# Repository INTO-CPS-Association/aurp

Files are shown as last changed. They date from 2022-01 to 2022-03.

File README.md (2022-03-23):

# Aarhus University Robotics Platform (AURP) Overview

## System
The system comprises:
- ODrive [D6374](https://eu.odriverobotics.com/shop/odrive-custom-motor-d6374-150kv) 150 KV BLDC motor
  - CUI [AMT102-V](https://www.cuidevices.com/product/resource/amt10.pdf) encoder - 8192 CPR quadrature with a single index mark
  - Thermistor (NTC 10k 1% 3435) thermally connected to motor windings to permit temperature monitoring
- ODrive [D5065](https://eu.odriverobotics.com/shop/odrive-custom-motor-d5065) 270 KV BLDC motor
  - CUI [AMT102-V](https://www.cuidevices.com/product/resource/amt10.pdf) encoder - 8192 CPR quadrature with a single index mark
  - Thermistor (NTC 10k 1% 3435) thermally connected to motor windings to permit temperature monitoring

_For detailed information on the D6374 and D5065 motors, see the [ODrive motor guide](https://docs.google.com/spreadsheets/d/12vzz7XVEK6YNIOqH0jAz51F5VUpc-lJEs3mmkWP1H4Y/edit#gid=0) ([PDF export](https://github.com/INTO-CPS-Association/aurp/blob/main/resources/ODrive_motor_guide.pdf) from 23-03-2022)_

- ODrive [V3.6 control board](https://eu.odriverobotics.com/shop/odrive-v36) - 56 V with connectors
  - 50 W power resistor (measured resistance of 2 &Omega;)
  - 2x Noctua [NF-A4x20 5V PWM](https://noctua.at/en/products/fan/nf-a4x20-5v-pwm) fan
- Mean Well [UHP-1000-48](https://www.meanwell.com/webapp/product/search.aspx?prod=UHP-1000) 1000 W / 48 V DC (21 A) power supply configured with 3x XT-60 connectors

<p align="center">
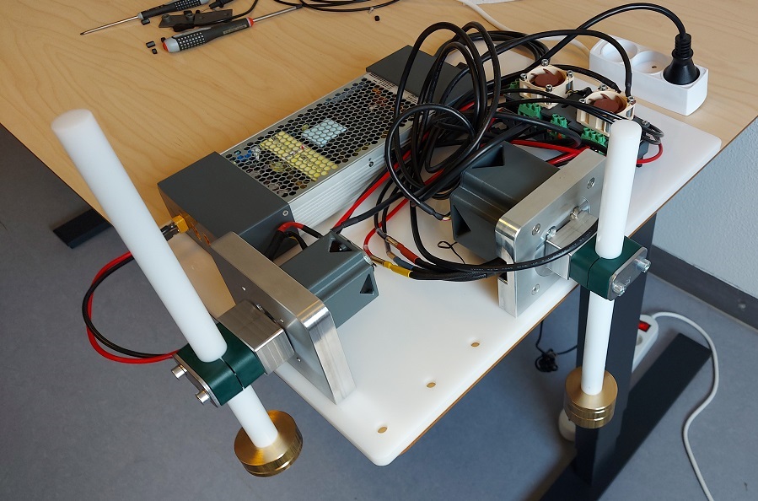
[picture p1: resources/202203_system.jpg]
The system as of March 2022
  
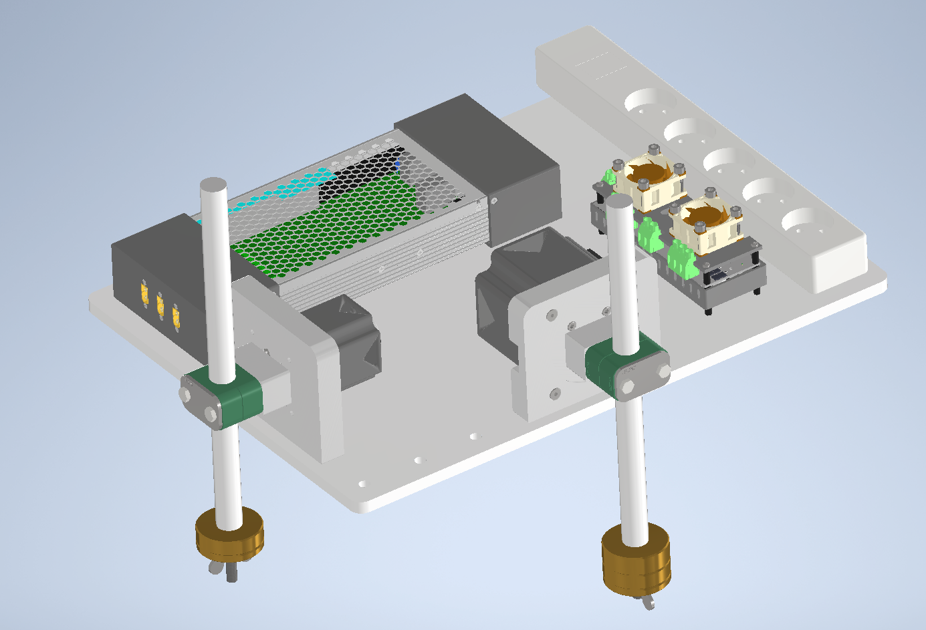
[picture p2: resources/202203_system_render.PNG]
A render of the system as of March 2022
  
</p>

## USB driver permissions

```
echo 'SUBSYSTEM=="usb", ATTR{idVendor}=="1209", ATTR{idProduct}=="0d[0-9][0-9]", MODE="0666"' | sudo tee /etc/udev/rules.d/50-odrive.rules
sudo udevadm trigger
```

Then reconnect the odrive usb cable

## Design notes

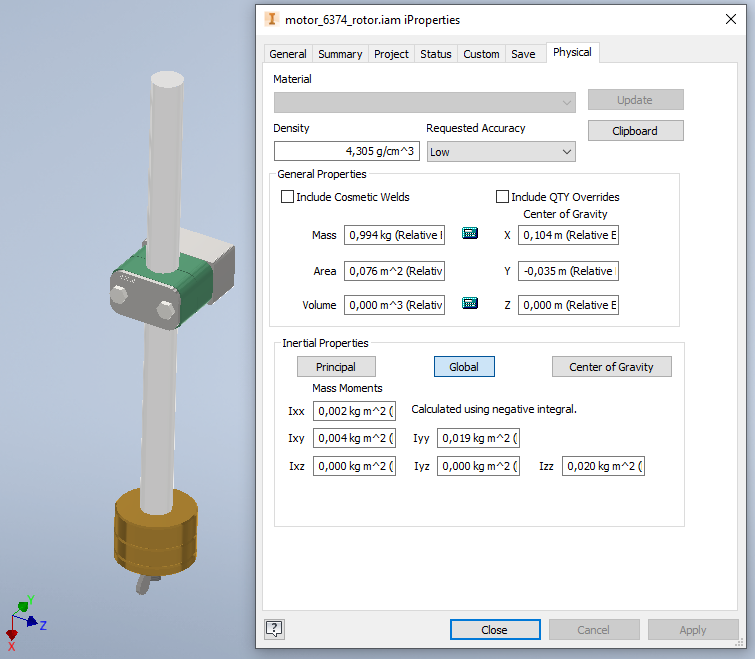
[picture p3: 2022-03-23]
resources/motor_D6374_rotor_inertia.PNG

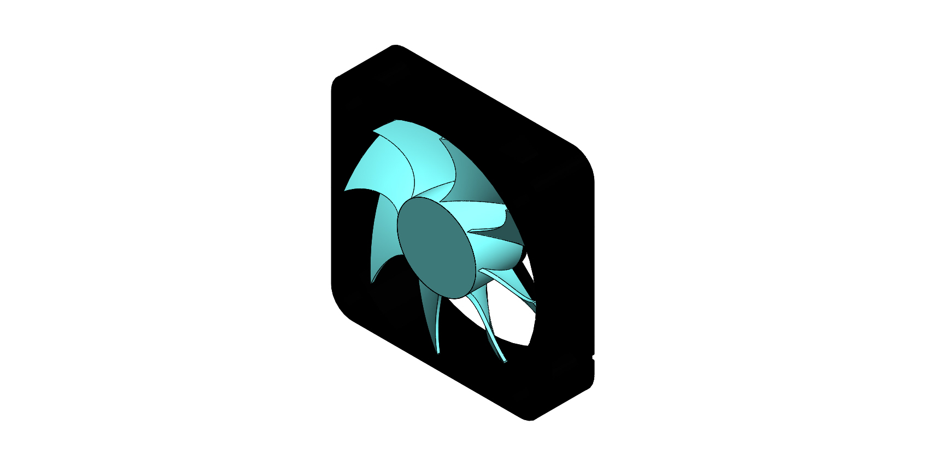
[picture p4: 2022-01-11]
cad/Control_Board/dc-fan-4.snapshot.2/DC Fan(40X40).JPG

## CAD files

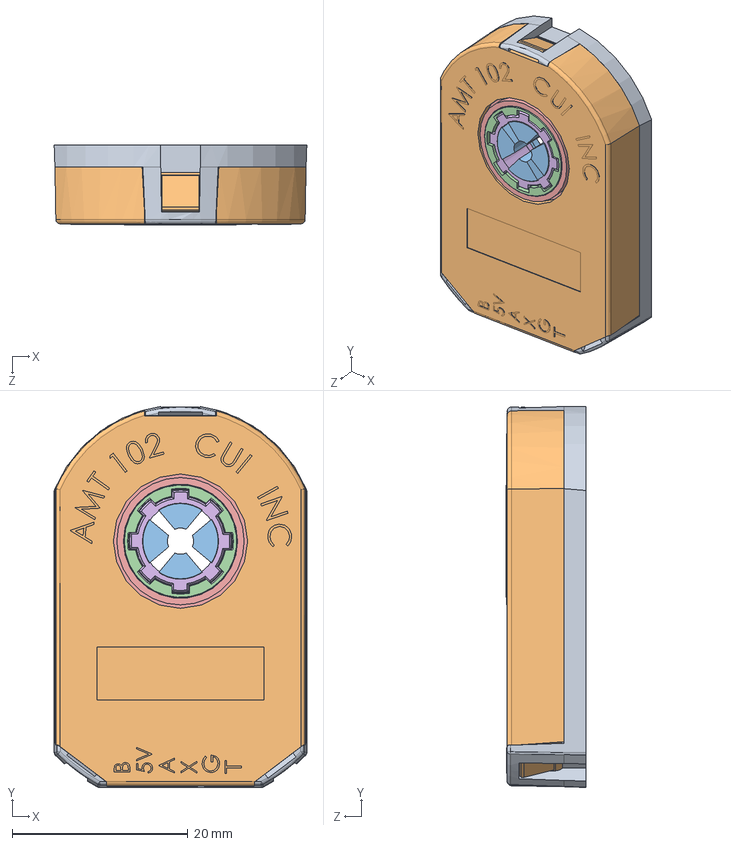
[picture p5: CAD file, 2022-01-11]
cad/Encoder_CUI_AMT_102/amt102-v.SLDASM
28.8 x 43.4 x 9.15 mm
amt102-v_01
amt102-v_02
amt102-v_03
amt102-v_04
amt102-v_05
amt102-v_06
amt102-v_07
amt102-v_08
amt102-v_09
amt102-v_10
amt102-v_11
amt102-v_12
amt102-v_13
amt102-v_14
amt102-v_15

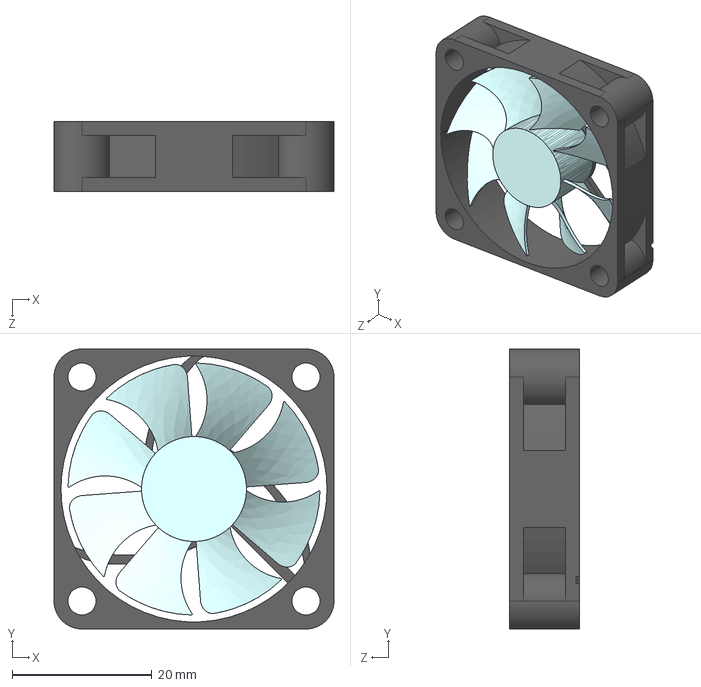
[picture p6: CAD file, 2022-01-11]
cad/Control_Board/dc-fan-4.snapshot.2/DC Fan(40X40).STEP
40.0 x 40.0 x 10.0 mm
DC Fan(40X40) Part1
DC Fan(40X40) Part2

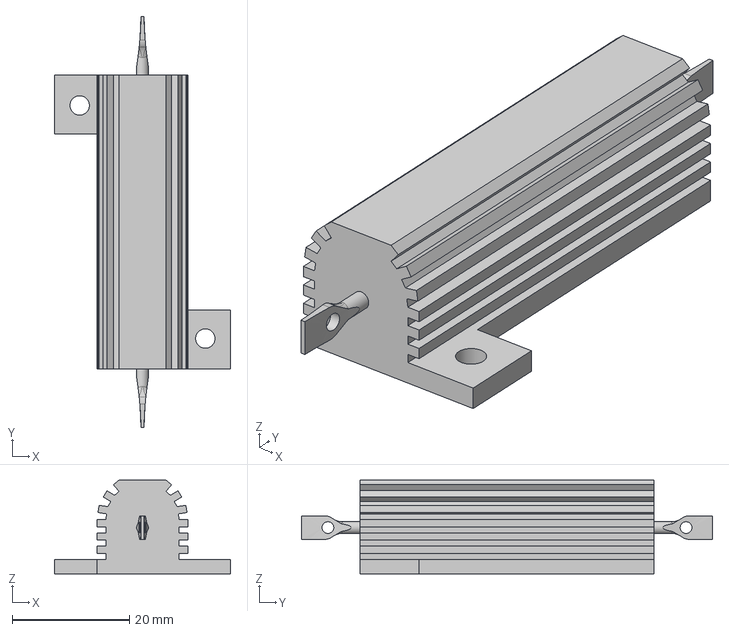
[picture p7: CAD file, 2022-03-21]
cad/Control_Board/power_resistor_THS50.step
30.0 x 70.0 x 16.0 mm

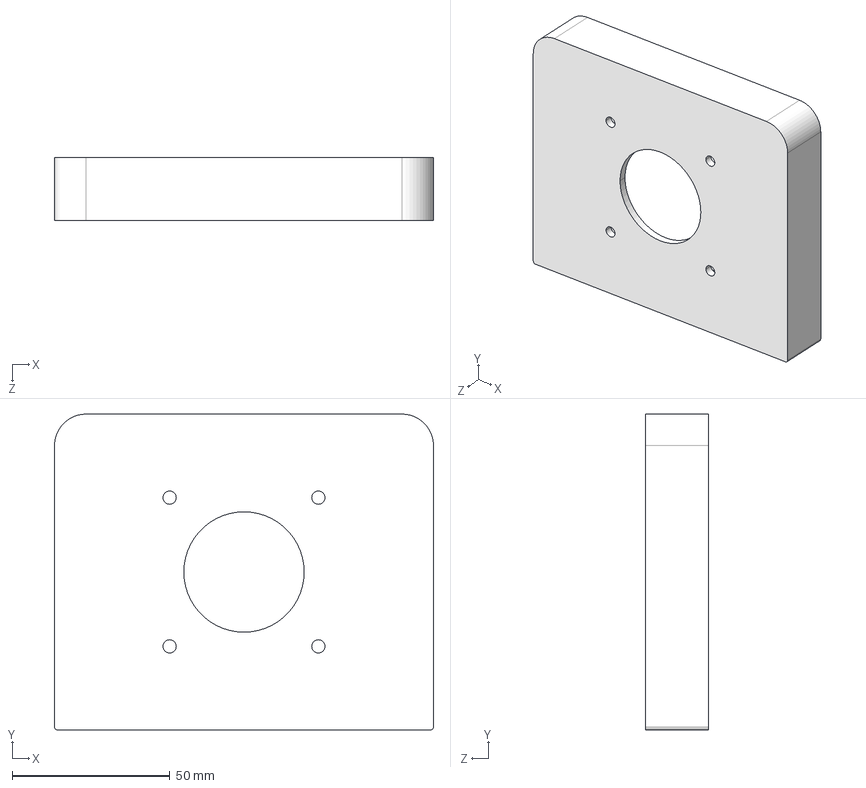
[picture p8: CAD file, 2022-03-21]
cad/D5065_Enclosure/Bracket_D5065.STEP
120.0 x 100.0 x 20.0 mm

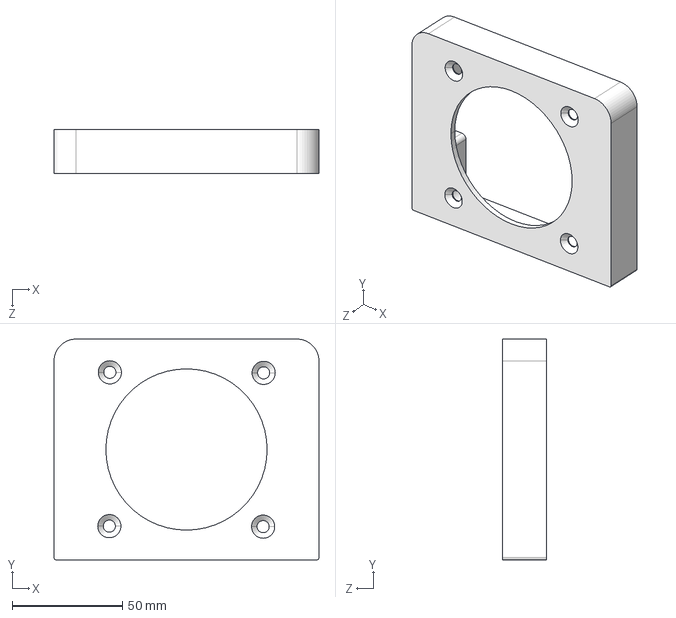
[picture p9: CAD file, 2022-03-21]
cad/D6374_Enclosure/bracket_D6374.STEP
120.0 x 100.0 x 20.0 mm

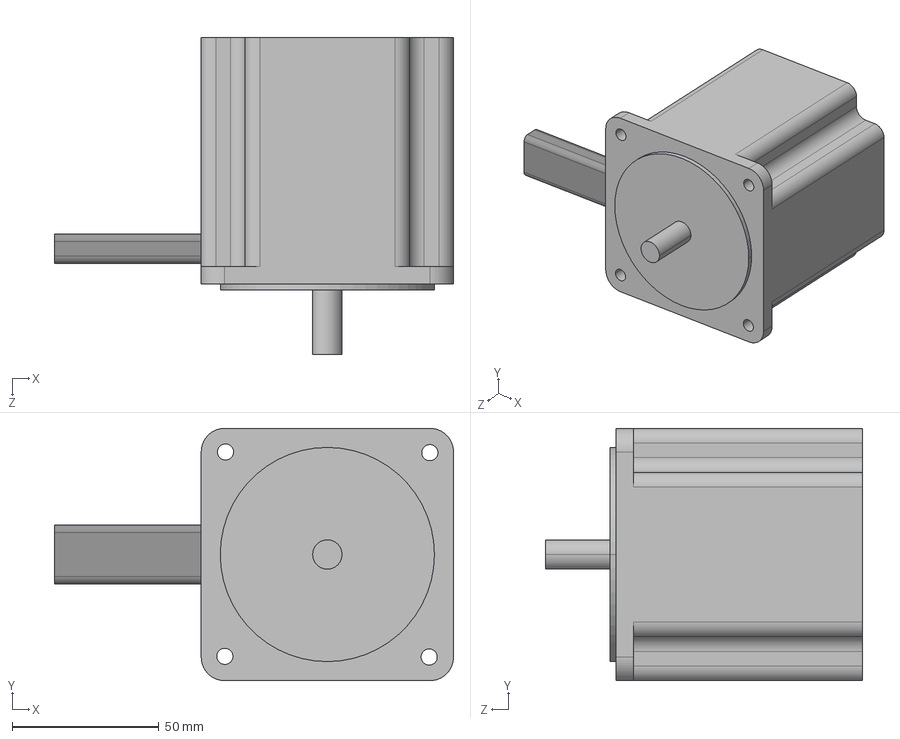
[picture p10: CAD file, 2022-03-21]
cad/Motor10mm.STEP
136.0 x 86.0 x 108.0 mm

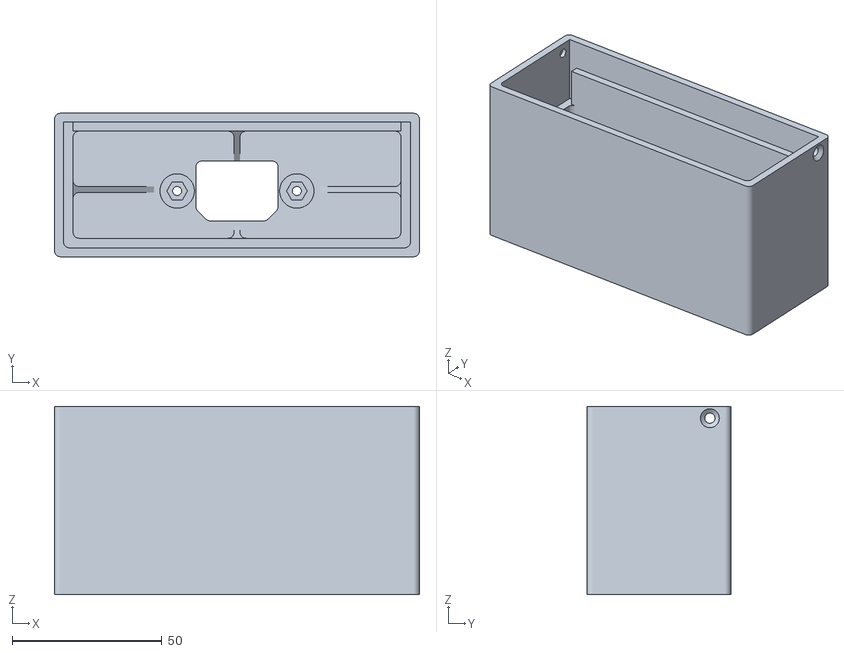
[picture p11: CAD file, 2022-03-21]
cad/PSU/high_voltage_cover.stl
122.0 x 48.0 x 63.0

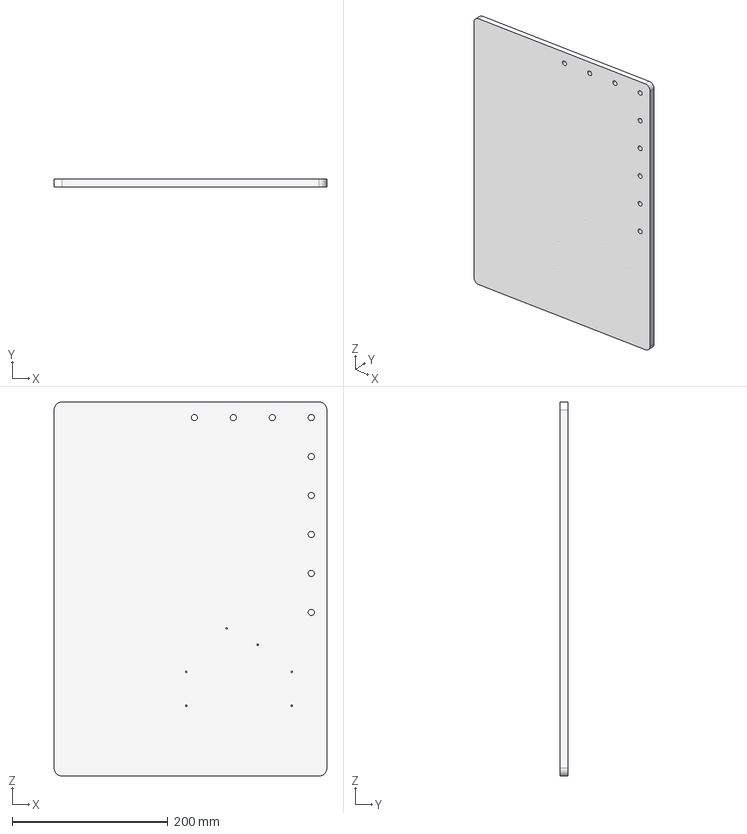
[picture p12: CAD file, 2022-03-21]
cad/bottom_plate.stp
350.0 x 10.0 x 480.0 mm

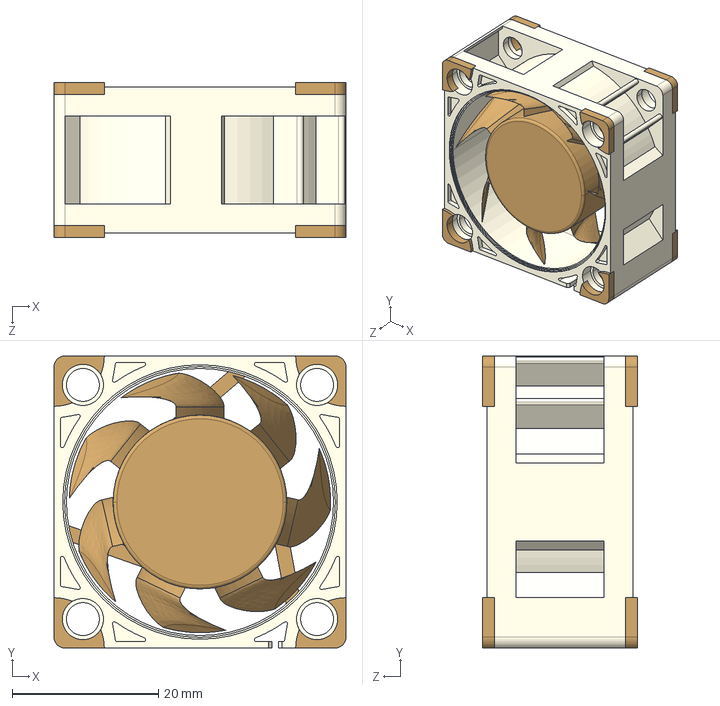
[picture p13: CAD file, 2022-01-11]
cad/Control_Board/NF-A4X20_5V_PWM.STEP
39.9 x 39.9 x 21.1 mm

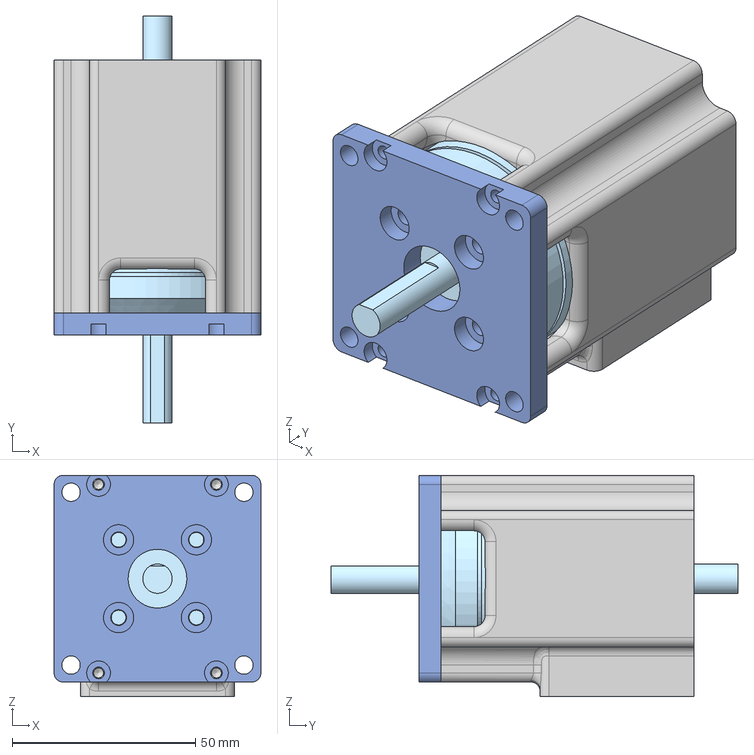
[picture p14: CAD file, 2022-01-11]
cad/D5065_Enclosure/Enclosure_Forced_Air.step
56.4 x 111.0 x 60.4 mm

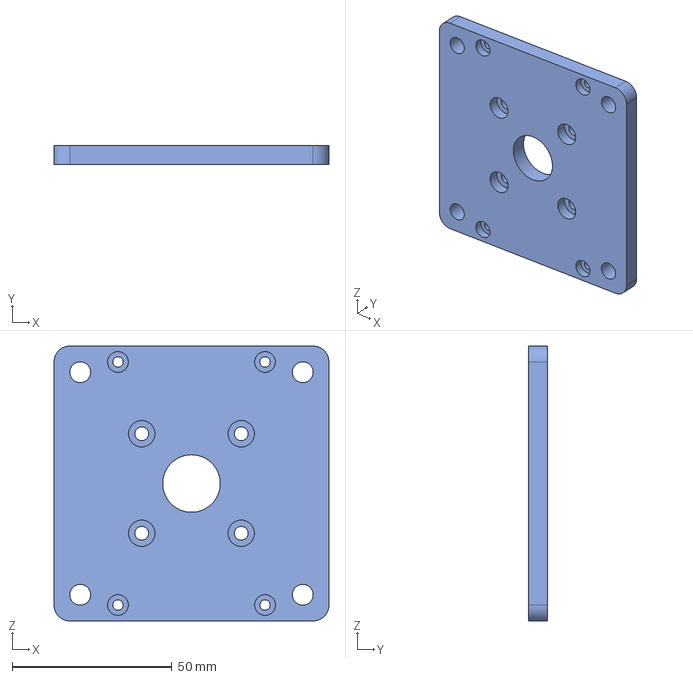
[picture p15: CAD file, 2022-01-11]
cad/D6374_Enclosure/Enclosure_Plate.step
86.0 x 6.00 x 86.0 mm

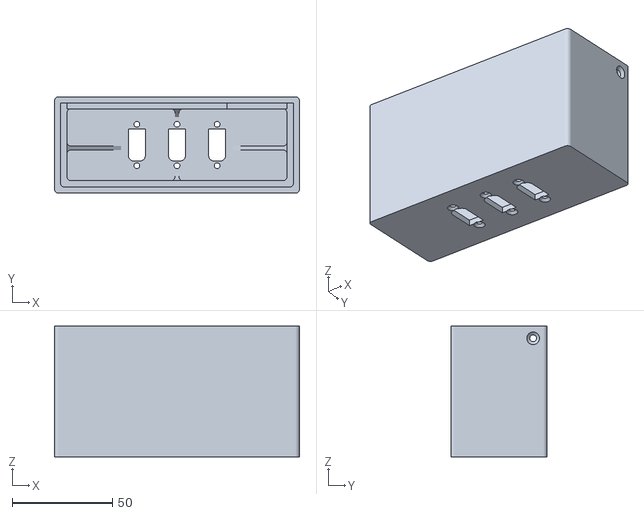
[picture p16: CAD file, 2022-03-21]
cad/PSU/low_voltage_cover.stl
122.0 x 48.0 x 65.0

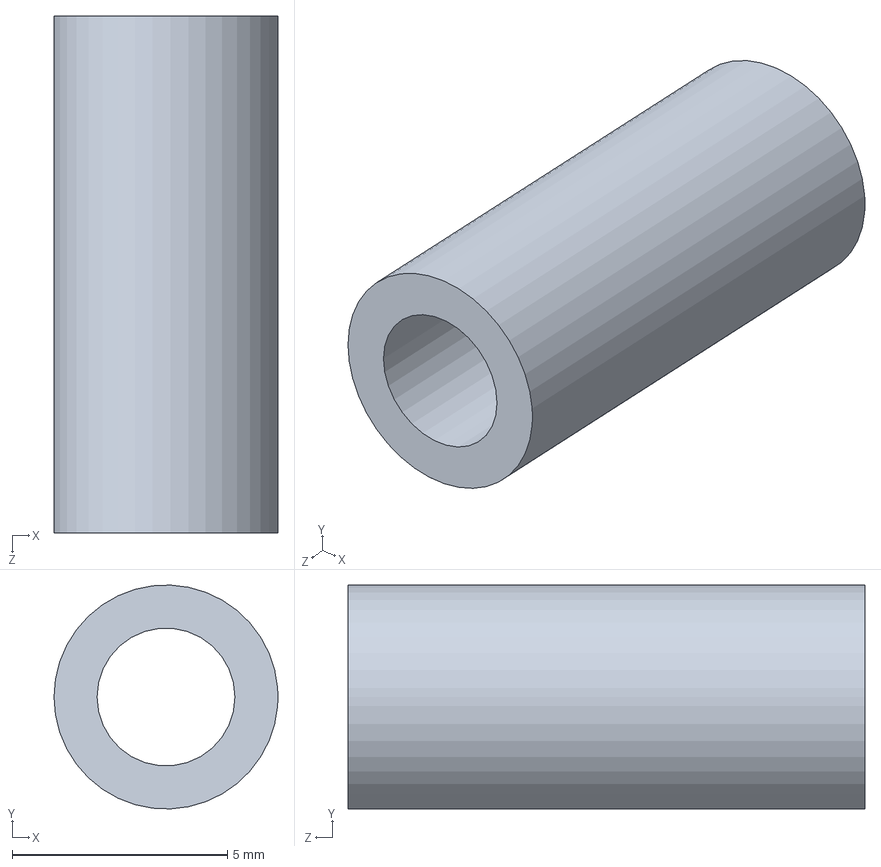
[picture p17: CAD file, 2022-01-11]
cad/Control_Board/fakespacer.SLDPRT
5.20 x 5.20 x 12.0 mm

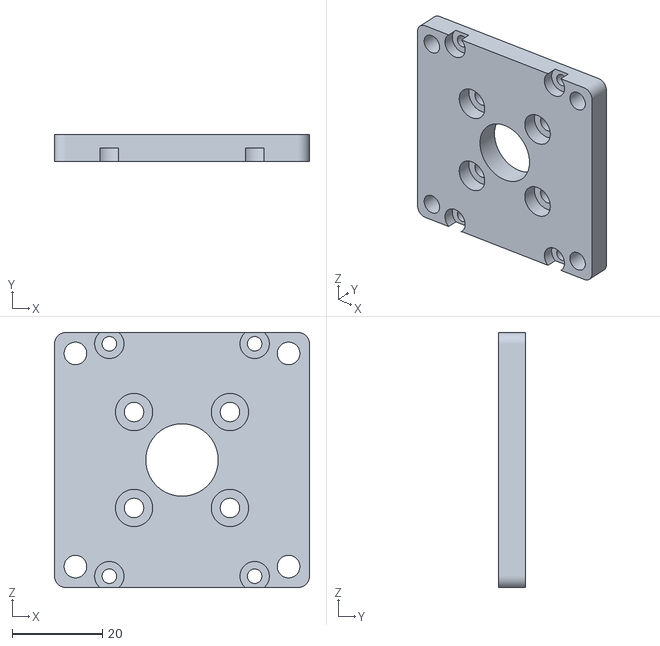
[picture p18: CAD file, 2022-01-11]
cad/D5065_Enclosure/Enclosure_Plate.stl
56.4 x 6.00 x 56.4

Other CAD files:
cad/D6374_Enclosure/Enclosure_Forced_Air.step
cad/power_strip.step
cad/PSU/high_voltage_cover_tc2_v2.stl
cad/axle_tube_mount_10mm.stp
cad/320_pp-dp-as_m_w1.stp
cad/Control_Board/caseBot.SLDPRT
cad/Control_Board/casetop.SLDPRT
cad/Control_Board/dc-fan-4.snapshot.2/DC Fan(40X40).SLDASM
cad/D5065_Enclosure/Enclosure_Natural_Cooling.step
cad/D6374_Enclosure/Enclosure_Natural_Cooling.step
cad/D6374_Enclosure/Enclosure_Plate.stl
cad/Encoder_CUI_AMT_102/AMT-B0-W.SLDPRT
cad/Encoder_CUI_AMT_102/amt102-v_01.SLDPRT
cad/Encoder_CUI_AMT_102/amt102-v_02.SLDPRT
cad/Encoder_CUI_AMT_102/amt102-v_03.SLDPRT
cad/Encoder_CUI_AMT_102/amt102-v_04.SLDPRT
cad/Encoder_CUI_AMT_102/amt102-v_05.SLDPRT
cad/Encoder_CUI_AMT_102/amt102-v_06.SLDPRT
cad/Encoder_CUI_AMT_102/amt102-v_07.SLDPRT
cad/Encoder_CUI_AMT_102/amt102-v_08.SLDPRT
cad/Encoder_CUI_AMT_102/amt102-v_09.SLDPRT
cad/Encoder_CUI_AMT_102/amt102-v_10.SLDPRT
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

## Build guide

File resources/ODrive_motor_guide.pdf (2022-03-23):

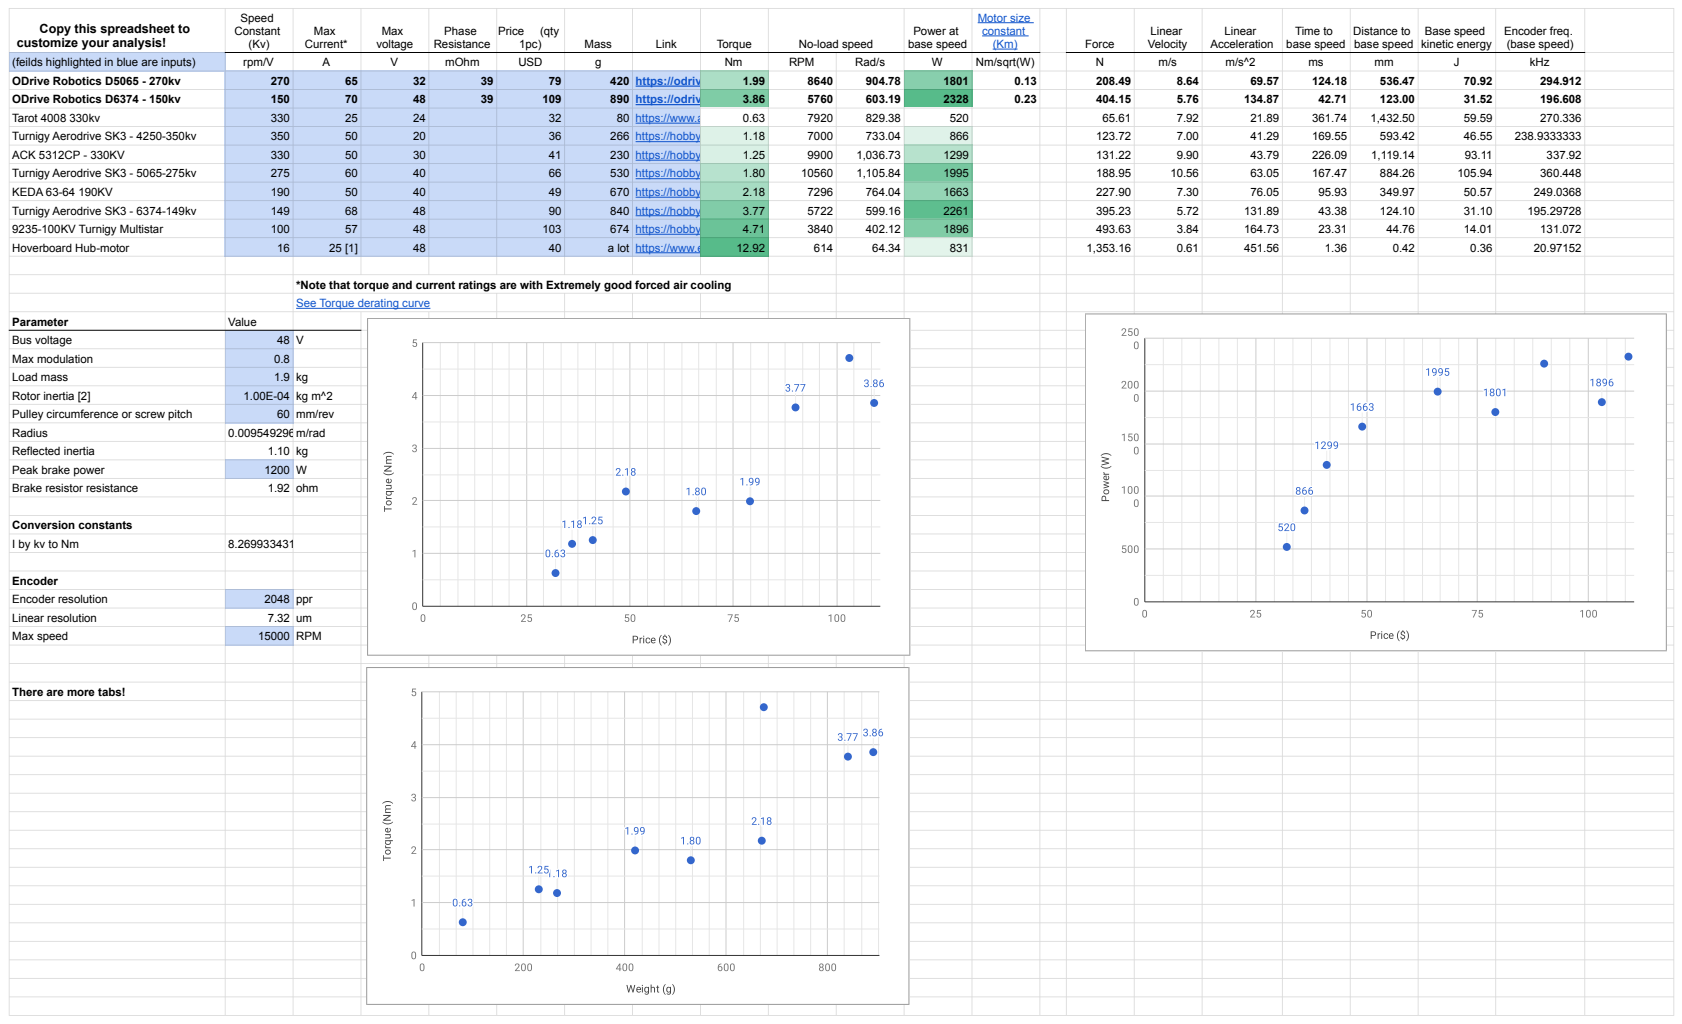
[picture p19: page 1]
Speed Constant; Max Current*; Max voltage; Phase Resistance; Price; (qty; Mass; Link; Torque; No-load speed; Power at base speed; Motor size constant; Force; Linear Velocity; Linear Acceleration; Time to base speed; Distance to base speed; Base speed kinetic energy; Encoder freq. (base speed); (feilds highlighted in blue are inputs); rpm/V; mOhm; USD; RPM; Rad/s; Nm/sqrt(W); kHz; ODrive Robotics D5065 - 270kv; 420 https://odriverobotics.com/shop/odrive-custom-motor-d5065 1.99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

Copy this spreadsheet to
customize your analysis! 📚📐📏

*Note that torque and current ratings are with Extremely good forced air cooling
See Torque derating curve

There are more tabs!

Speed | Forced air | Good airflow | No airflow
0.025 | 1 | 0.5 | 0.3

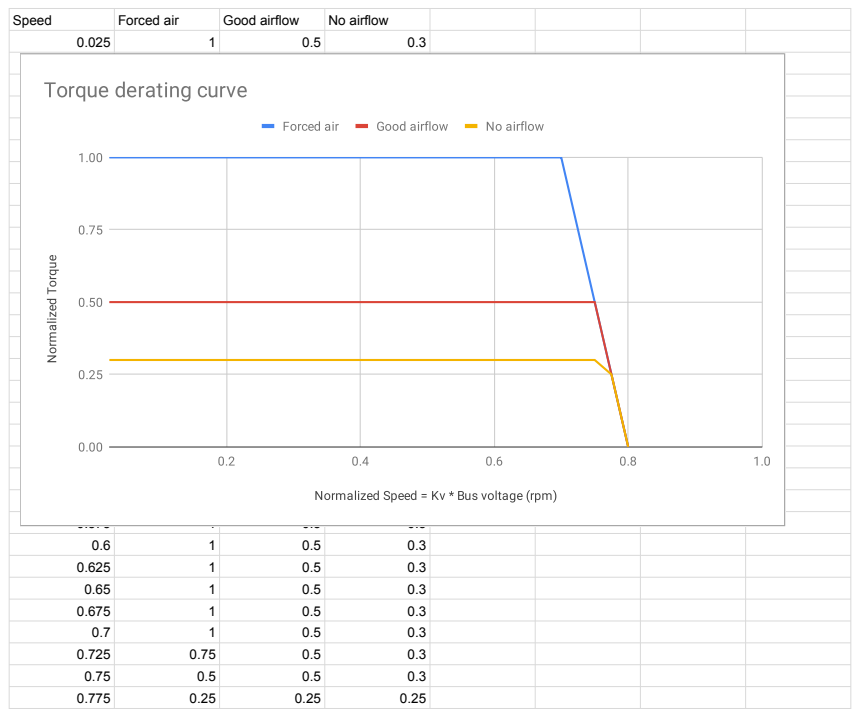
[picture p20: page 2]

0.8 | 0 | 0 | 0

0.825

0.85

0.875

0.9

0.925

0.95

0.9751

Rotor mass | Rotor diameter | Shaft length | Shaft diameter | Shaft density | Shaft mass | Shaft MoI | End Face thickness | End face density | End face mass | End Face MoI | Rotor casing mass | Rotor casing MoI | Total MoI
g | mm | mm | mm | kg/m^3 | g | kg*m^2 | mm | kg/m^3 | g | kg*m^2 | g | kg*m^2 | kg*m^2
Red 5065 | 190 | 50 | 83 | 8 | 7850 | 32.7504751 5.24E-07 | 7.5 | 1350 | 19.880391016.21E-06 | 137.36913398.59E-05 | 9.26E-05

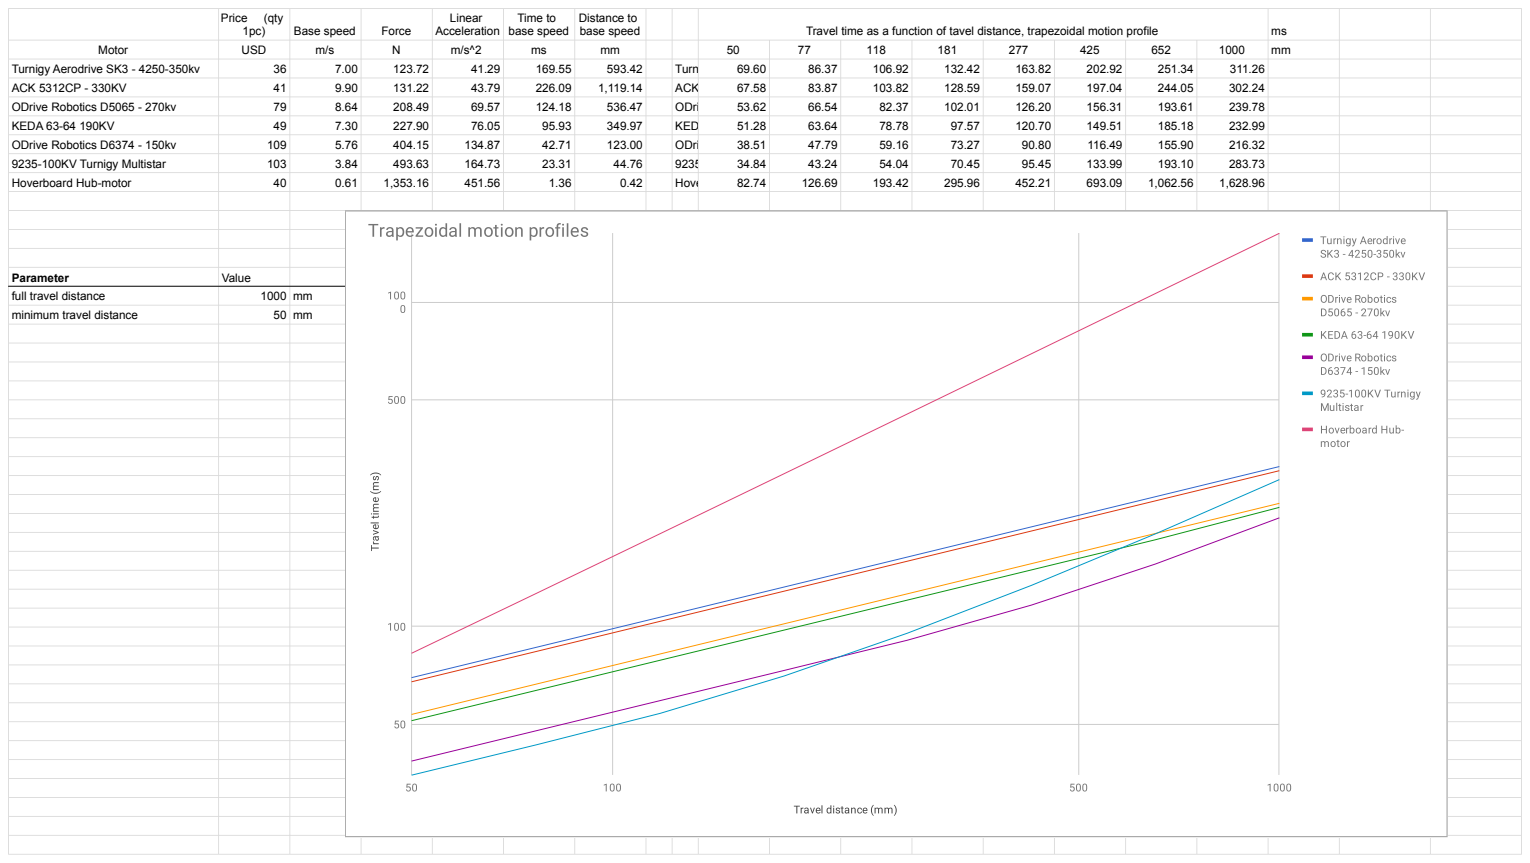
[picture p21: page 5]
Price; (qty; Base speed; Force; Linear Acceleration; Time to base speed; Distance to; base speed; Travel time as a function of tavel distance, trapezoidal motion profile; Motor; USD; Turnigy Aerodrive SK3 - 4250-350kv; Turnigy Aerodrive SK3 - 4250-350kv 69.60; ACK 5312CP - 330KV; ACK 5312CP - 330KV 67.58; ODrive Robotics D5065 - 270kv; ODrive Robotics D5065 - 270kv 53.62; KEDA 63-64 190KV; KEDA 63-64 190KV 5.28; ODrive Robotics D6374 - 150kv; ODrive Robotics D6374 - 150kv 38.51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

## Speed Constant

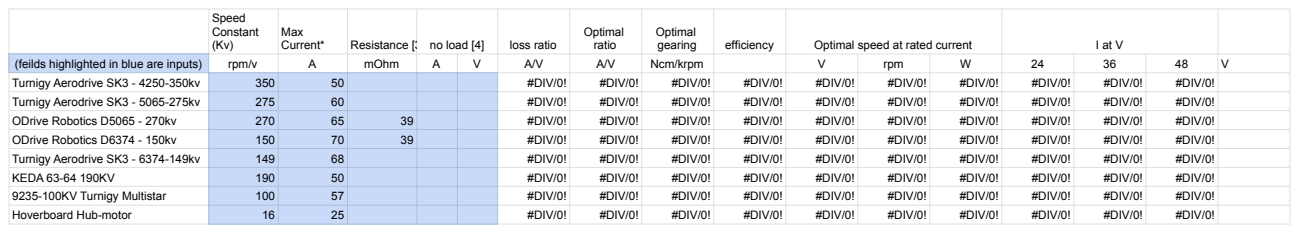
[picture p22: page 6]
Max; Current*; Resistance [3] no load [4]; loss ratio; Optimal ratio; Optimal; gearing; efficiency; Optimal speed at rated current; (feilds highlighted in blue are inputs); rpm/v; mOhm; Ncm/krpm; rpm; Turnigy Aerodrive SK3 - 4250-350kv; #DIV/0!; Turnigy Aerodrive SK3 - 5065-275kv; ODrive Robotics D5065 - 270kv; ODrive Robotics D6374 - 150kv; Turnigy Aerodrive SK3 - 6374-149kv; KEDA 63-64 190KV; 9235-100KV Turnigy Multistar; Hoverboard Hub-motor

# [1] Assuming improved cooling mod

[2] Note: We should measure inertia of each individual motor. This is an estimate of 5065 size motors.

# [3] Data from https://www.ecalc.ch/motorcalc.php, high accuracy not guaranteed

# [4] Data from https://www.ecalc.ch/motorcalc.php, high accuracy not guaranteed

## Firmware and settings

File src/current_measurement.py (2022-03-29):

from time import sleep, time
import numpy as np
import matplotlib.pyplot as plt
import pandas as pd
import math

import odrive
from odrive.enums import (
    AXIS_STATE_FULL_CALIBRATION_SEQUENCE,
    AXIS_STATE_IDLE,
    AXIS_STATE_ENCODER_INDEX_SEARCH,
    AXIS_STATE_CLOSED_LOOP_CONTROL,
    CONTROL_MODE_TORQUE_CONTROL,
    CONTROL_MODE_POSITION_CONTROL,
    INPUT_MODE_PASSTHROUGH,
)
from utils import assert_no_errors

if __name__ == "__main__":
    # CLEAR
    # try:
    #     odrv0 = odrive.find_any()
    #     odrv0.erase_configuration()
    # except odrive.fibre.libfibre.ObjectLostError:
    #     pass
    odrv0 = odrive.find_any()
    assert_no_errors(odrv0, "initial")

    # BRAKE
    odrv0.config.enable_brake_resistor = True
    odrv0.config.brake_resistance = 2.2  # [A]
    odrv0.axis0.motor.config.torque_constant = 8.27 / 150

    # configuration must be saved otherwise the error "MOTOR_ERROR_BRAKE_RESISTOR_DISARMED" is emitted
    try:
        odrv0.save_configuration()
    except odrive.fibre.libfibre.ObjectLostError:
        pass

    odrv0 = odrive.find_any()

    # CALIBRATION
    # odrv0.axis0.encoder.config.use_index = True
    # odrv0.axis0.requested_state = AXIS_STATE_FULL_CALIBRATION_SEQUENCE

    # while odrv0.axis0.current_state != AXIS_STATE_IDLE:
    #     sleep(0.1)

    # assert_no_errors(odrv0, "calibration")

    # odrv0.axis0.encoder.config.pre_calibrated = True
    odrv0.axis0.motor.config.pre_calibrated = True

    # INDEX SEARCH
    odrv0.axis0.requested_state = AXIS_STATE_ENCODER_INDEX_SEARCH
    while odrv0.axis0.current_state != AXIS_STATE_IDLE:
        sleep(0.1)
    assert_no_errors(odrv0, "index search")

    odrv0.axis0.requested_state = AXIS_STATE_CLOSED_LOOP_CONTROL
    odrv0.axis0.controller.config.control_mode = CONTROL_MODE_POSITION_CONTROL
    odrv0.axis0.controller.config.input_mode = INPUT_MODE_PASSTHROUGH
    odrv0.axis0.controller.config.vel_limit = 5.0

    sleep(1.0)

    assert_no_errors(odrv0, "torque control")

    t_sample = 0.001
    t_cur = 0.0
    t_end = 5.0
    t_last = t_cur
    t_offset = time()
    current_estimate = []
    t = []
    position_setpoint = []
    position_estimate = []
    velocity_setpoint = []
    velocity_estimate = []
    torque_setpoint = []

    def pos_setpoint_t(t):
        return math.sin(0.05 * t_end * t**3 + 2 * t) * 0.5

    def torque_setpoint_t(t):
        if t < 1:
            return 0.5
        else:
            return 1.0

    while t_cur < t_end:

        assert_no_errors(odrv0, f"torque control at t={t_cur}")

        if (t_cur - t_last) >= t_sample:
            odrv0.axis0.controller.input_pos = pos_setpoint_t(t_cur)
            t.append(t_cur)

            position_estimate.append(odrv0.axis0.encoder.pos_estimate)
            velocity_estimate.append(odrv0.axis0.encoder.vel_estimate)
            current_estimate.append(odrv0.axis0.motor.current_control.Iq_measured)

            position_setpoint.append(odrv0.axis0.controller.pos_setpoint)
            velocity_setpoint.append(odrv0.axis0.controller.vel_setpoint)
            torque_setpoint.append(odrv0.axis0.controller.torque_setpoint)

            t_last = t_cur

        t_cur = time() - t_offset

    # convert to np arrays
    torque_estimated = (
        np.array(current_estimate) * odrv0.axis0.motor.config.torque_constant
    )
    current_setpoint = (
        np.array(torque_setpoint) / odrv0.axis0.motor.config.torque_constant
    )
    t = np.array(t) - np.min(t)
    position_estimate = np.array(position_estimate)

    # export
    d = {
        "timestamp": t,
        "actual_q_0": position_estimate * 2 * np.pi,
        "actual_current_0": current_estimate,
    }

    df = pd.DataFrame(data=d)
    df.to_csv("onelink_data.csv", sep=" ", index=False)

    # plotting

    fig, ax = plt.subplots()
    ax.plot(t, current_estimate, marker="*")
    ax.set_xlabel("t[s]")
    ax.set_ylabel("i(t)[A]")

    fig, (ax1, ax2, ax3) = plt.subplots(3, 1, sharex=True)

    ax1.plot(t, position_estimate, label="estimated")
    ax1.plot(t, position_setpoint, label="setpoint")
    ax1.set_ylabel("position(t) [turns]")

    ax2.plot(t, velocity_estimate, label="estimated")
    ax2.plot(t, velocity_setpoint, label="setpoint")
    ax2.axhline(odrv0.axis0.controller.config.vel_limit, color="green")
    ax2.set_ylabel("velocity(t) [turns/s]")

    ax3.plot(t, current_estimate, label="estimated")
    ax3.plot(t, current_setpoint, label="setpoint")
    ax3.axhline(odrv0.axis0.motor.config.current_lim, color="green", label="limit")
    ax3.set_xlabel("t[s]")
    ax3.set_ylabel("current(t) [A]")
    ax3.legend()

    plt.show()

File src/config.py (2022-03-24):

# In this script, the configuration settings of the AURP are specified.
# Make sure that the hardware connected to the ODrive control board 
# corresponds to the specifications in the script.

import odrive
from odrive.enums import MOTOR_TYPE_HIGH_CURRENT

def configure_odrive():
    od = odrive.find_any()
    try:
        od.erase_configuration()
    except odrive.fibre.libfibre.ObjectLostError:
        pass
    try:
        od = odrive.find_any()
        od.reboot()
    except odrive.fibre.libfibre.ObjectLostError:
        pass
    od = odrive.find_any()

    print("Configuring ODrive...")

    # ============= Brake Resistor =================
    od.config.enable_brake_resistor = True
    od.config.brake_resistance = 2.2  # [A]

    # ================= Axis 0 =====================
    # SMALL (270 KV) MOTOR
    # od.axis0.motor.config.torque_constant = 8.27 / 270  # [Nm/A]
    # od.axis0.motor.config.motor_type = MOTOR_TYPE_HIGH_CURRENT
    # od.axis0.controller.config.vel_limit = 2.0  # [turns/s]
    # od.axis0.motor.config.current_lim = 30.0  # [A]
    # od.axis0.motor.config.pole_pairs = 7  # [-]
    # od.axis0.encoder.config.cpr = 8192  # [counts per revolution]
    # od.axis0.motor.config.calibration_current = 15.0  # [A]
    # od.axis0.encoder.config.use_index = True
    # od.axis0.config.startup_encoder_index_search = True

    # ================= Axis 1 =====================
    # LARGE (150 KV) MOTOR
    od.axis0.motor.config.torque_constant = 8.27 / 150  # [Nm/A]
    od.axis0.motor.config.motor_type = MOTOR_TYPE_HIGH_CURRENT
    od.axis0.controller.config.vel_limit = 2.0  # [turns/s]
    od.axis0.motor.config.current_lim = 30.0  # [A]
    od.axis0.motor.config.pole_pairs = 7  # [-]
    od.axis0.encoder.config.cpr = 8192  # [counts per revolution]
    od.axis0.motor.config.calibration_current = 15.0  # [A]
    od.axis0.encoder.config.use_index = True

    # od.save_configuration()

    print("ODrive configured successfully.")
    return od

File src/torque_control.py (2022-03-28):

import odrive
from odrive.enums import AXIS_STATE_FULL_CALIBRATION_SEQUENCE, AXIS_STATE_CLOSED_LOOP_CONTROL, MOTOR_TYPE_HIGH_CURRENT, AXIS_STATE_IDLE, AXIS_STATE_ENCODER_INDEX_SEARCH, CONTROL_MODE_TORQUE_CONTROL, INPUT_MODE_PASSTHROUGH
import numpy as np
import time
import math
import matplotlib.pyplot as plt
from utils import assert_no_errors
from time import sleep

# CLEAR
try:
    odrv0 = odrive.find_any()
    odrv0.erase_configuration()
except odrive.fibre.libfibre.ObjectLostError:
    pass
odrv0 = odrive.find_any()
assert_no_errors(odrv0,"initial")

# BRAKE
odrv0.config.enable_brake_resistor = True
odrv0.config.brake_resistance = 2.2  # [A]

# configuration must be saved otherwise the error "MOTOR_ERROR_BRAKE_RESISTOR_DISARMED" is emitted
try:
    odrv0.save_configuration()
except odrive.fibre.libfibre.ObjectLostError:
    pass

odrv0 = odrive.find_any()

# CALIBRATION
odrv0.axis0.encoder.config.use_index = True
odrv0.axis0.requested_state = AXIS_STATE_FULL_CALIBRATION_SEQUENCE

while(odrv0.axis0.current_state != AXIS_STATE_IDLE):
    sleep(0.1)

assert_no_errors(odrv0,"calibration")

odrv0.axis0.encoder.config.pre_calibrated = True
odrv0.axis0.motor.config.pre_calibrated = True

# INDEX SEARCH
odrv0.axis0.requested_state = AXIS_STATE_ENCODER_INDEX_SEARCH
while(odrv0.axis0.current_state != AXIS_STATE_IDLE):
    sleep(0.1)
assert_no_errors(odrv0,"index search")
    

odrv0.axis0.requested_state = AXIS_STATE_CLOSED_LOOP_CONTROL
odrv0.axis0.controller.config.control_mode = CONTROL_MODE_TORQUE_CONTROL

odrv0.axis0.controller.input_torque = 1.0

assert_no_errors(odrv0,"torque control")

odrv0.axis0.controller.config.input_mode = INPUT_MODE_PASSTHROUGH
odrv0.axis0.controller.config.vel_limit = 20.0  # [turns/s]
# Torque Controller
inertia_rotor = 1E-4  # inertia of the D5053 rotor according to ODrive
inertia_pendulum = 0.001 # 0.019  # inertia of rod with attached weights of 250 g + 200 g + 100 g = 550 g offset X mm
odrv0.axis0.controller.config.inertia = inertia_rotor + inertia_pendulum
K_tau = 8.27 / 150
odrv0.axis0.motor.config.torque_constant = K_tau 


t_cur = time.time()
t_start = t_cur
t_sample_last = time.time()
t_setpoint_last = time.time()
dt_sample_target = 1e-4
dt_setpoint_target = 1e-4 / 3  # 3 kHz torque control
timestamp_sample = []
timestamp_setpoint = []
q = []
q_setpoint = []
qd = []
qd_setpoint = []
tau = []
tau_setpoint = []
t_duration = 5.0

# Position and velocity trajectories
def pos_setpoint(t):
    return math.sin(0.05*t_duration*t**3 + 2*t)*0.5 + 0.5

def vel_setpoint(t):
    return math.cos(0.05*t_duration*t**3 + 2*t)*0.025*t**3  # derivative of pos_setpoint



Kp = 3*10
Kd = 2
tau_lim = 3.5  # [Nm] Torque limit (D6374 is rated for 3.86 Nm)
def pd_control(err_pos, err_vel):
    tau = Kp*err_pos + Kd*err_vel
    return np.clip(tau, -tau_lim, tau_lim) # saturate output for safety

while True:
    t_cur = time.time()

    assert_no_errors(odrv0,"torque control")

    # Update controller values
    if t_cur - t_setpoint_last >= dt_setpoint_target:
        t_setpoint_last = t_cur
        q_err = pos_setpoint(t_cur - t_start) - odrv0.axis0.encoder.pos_estimate
        qd_err = vel_setpoint(t_cur - t_start) - odrv0.axis0.encoder.vel_estimate
        tauu = pd_control(q_err, qd_err)
        odrv0.axis0.controller.input_torque = tauu

        timestamp_setpoint.append(t_cur)
        q_setpoint.append(pos_setpoint(t_cur - t_start))
        qd_setpoint.append(vel_setpoint(t_cur - t_start))
        tau_setpoint.append(tauu)

    # Sample measured data
    if t_cur - t_sample_last >= dt_sample_target:
        t_sample_last = t_cur
        timestamp_sample.append(t_cur)
        q.append(odrv0.axis0.encoder.pos_estimate)
        qd.append(odrv0.axis0.encoder.vel_estimate)
        tau.append(odrv0.axis0.motor.current_control.Iq_measured*K_tau)
        
    if t_cur - t_start > t_duration:
        break

odrv0.axis0.controller.input_torque = 0.0


timestamp_sample = np.array(timestamp_sample)
timestamp_setpoint = np.array(timestamp_setpoint)
q = np.array(q)
q_setpoint = np.array(q_setpoint)
qd = np.array(qd)
qd_setpoint = np.array(qd_setpoint)
tau = np.array(tau)
tau_setpoint = np.array(tau_setpoint)
dt_sample = timestamp_sample[1:] - timestamp_sample[:-1]
dt_setpoint = timestamp_setpoint[1:] - timestamp_setpoint[:-1]
timestamp_sample = timestamp_sample - t_start  # Zero timestamp
timestamp_setpoint = timestamp_setpoint - t_start  # Zero timestamp

fig, (ax1, ax2) = plt.subplots(2, 1, sharex=True)
ax1.plot(timestamp_sample, q, label="actual")
ax1.plot(timestamp_setpoint, q_setpoint, label="setpoint")
xmin = min(timestamp_sample[0], timestamp_setpoint[0])
xmax = max(timestamp_sample[0], timestamp_sample[-1])
ax1.set_xlim([timestamp_sample[0], timestamp_sample[-1]])
ax1.set_ylabel("Angular Position [turns]")
ax2.plot(timestamp_sample, tau, label="true")
ax2.plot(timestamp_sample,tau_setpoint, label="setpoint")
ax2.set_ylabel("Torque [Nm]")
ax2.set_xlabel("Time [s]")
ax2.legend()

fig, ax = plt.subplots()
ax.hist(dt_sample)
plt.xlabel('Time [s]')
plt.ylabel('Amount [-]')
plt.title('Sample Rate Histogram')


fig, ax = plt.subplots()
ax.hist(dt_setpoint)
plt.xlabel('Time [s]')
plt.ylabel('Amount [-]')
plt.title('Setpoint Update Rate Histogram')

plt.show()

# Generate CSV file with header (convert unit of q from [turns] to [rad])
sampled_data = np.array([timestamp_sample, q * 2*np.pi, tau])
header_txt = "timestamp actual_q_0 actual_current_0"
np.savetxt('onelink_data.csv', sampled_data, delimiter=' ', header=header_txt)

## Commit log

2022-01-11 added cad parts
    [AMT-B0-W.SLDPRT, AURP.0006.iam, DC Fan(40X40).SLDASM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]
2022-01-11 added test files for odrive
2022-03-21 updated cad models
    [320_pp-dp-as_m_w1.stp, Bracket_D5065.STEP, Motor10mm.STEP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]
2022-03-23 updated CAD models and pictures and removed OldVersions
    [axle_tube_mount_10mm.0004.dwg, axle_tube_mount_10mm.0004.ipt, axle_tube_mount_8mm.0003.ipt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]
2022-03-23 added Odrive motor guide PDF
2022-03-23 added mass properties for large motor rotor
2022-03-23 corrected position control mode
    [test.py]
2022-03-24 error: phase inductance out of range
    [calibration.py, config.py, test.py]
2022-03-25 non tested torque PD controller
2022-03-28 Add reset af brake configuration
    [calibration.py, experiment.py, reproduce.py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]
